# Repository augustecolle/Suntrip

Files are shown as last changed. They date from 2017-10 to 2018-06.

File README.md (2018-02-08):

# The Sun Trip
**Departure** mid june

**Deadline bike** february (preliminary inspection three months before departure, see Technical Regulations)

Auguste = :hear_no_evil:
Camille = :smirk_cat:
Baptist = :pig2:
Rien    = :car:
Mathieu = :construction_worker:

## Urgent TO DO's

1. ~~Start research on how to construct the roof :construction_worker:~~ DONE
2. ~~Do research on aerodynamic drag -- :hear_no_evil: :smirk_cat:~~ DONE
3. ~~Start research on best MPPT buck/boost converter for Li-ion technology -- :hear_no_evil:~~ DONE
4. Start research on batterypack -- :hear_no_evil:
3. ~~Make a technical drawing of frame :hear_no_evil: :smirk_cat:~~ DONE
4. ~~Read regulations in "Suntrip" folder -- :hear_no_evil: :smirk_cat:~~ DONE
5. ~~Order frame -- :hear_no_evil:~~ DONE
6. ~~present yourself :hear_no_evil:~~ DONE

## TO DO's

1. Compare different batteries on energy density (Wh/kg). Suntrip maximum 1100 Wh, 48 V.

   Nominal voltage as defined in datasheet, check if we can gain some capacity by choosing for the batteries with the lowest "nominal" voltage (a very underdefined term).

2. ~~Comparison of different solar panels.!~~ DONE

   Tandem regulations: max. 550 Wp and 3.05 m<sup>2</sup> __visible__. Max 1000 Wp in total. Working voltage must be <= 60 V.

3. ~~Passports: Each participant must hold before January 1st, 2018 a passport whose validity shall extend at least until February 1st, 2019.~~ DONE
 
4. Medical -- **before April 15th 2017** -- :hear_no_evil: :smirk_cat:

   - Obtain updated medical certificate in French or English confirming fitness for practice of endurance sports from a physician of their choice.

   - Signed medical record in annex of Adventure Regulations by our physician.

   - Vaccinations for travel in countries we will cross

5. Insurance (p23 of the Adventure Regulations)

6. Technical logbook (more info in early 2018).

7. Mapping an ideal route :hear_no_evil:

8. VISAs for all countries

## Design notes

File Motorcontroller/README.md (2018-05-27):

Motorcontroller
===============

I have to read much deeper into this matter but it seems like there are basically three options:

1. Trapezoidal control
2. Sinusoidal control
3. Field oriented control (a.k.a. the best in torque control and overall efficiency)

Phaserunner
-----------

The phaserunner looks like an evident choice, small, lightweight, state of the art, wide range of voltage and current, allows regenerative breaking, allows field weakening, ...

[check it here](http://www.ebikes.ca/product-info/phaserunner.html)

Fiel weakening test:

 - 12 amps field weakening gives 60 degrees Centigrade controller temperature and 18 amps phase current at no load. Motor goes from 41 km/h to 45.6 km/h no load speed.

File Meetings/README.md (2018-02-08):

Vergadering Soltech
-------------------
08/01/2018

Witruimte tussen cellen 2mm - max. 5mm meer opbrengst 2 a 3%

Plaatdikte te kiezen ifv sterkte/gewicht

Electronica minimale spanning voor te werken bepalend voor aantel seriecellen

Temperatuurscorrectie in MPPT voor batterijen laden?!

Cellen zelf solderen vs laten doen --> 200 euro

Solderen op ... 320? Vragen aan de fabrikant (SunPower)

Bypass diodes -> meer risicos bij laminatieproces want kabels moeten naar buiten gebracht worden

Misschien beter voor de hoeken, vooraan 6 -> 7 7 ... 7 -> 6 achteraan dan kunnen we hoeken afronden

Drie modules, 7 8 8 cellen op 7 cellen (breedte paneel).
-> 56 cellen 56 cellen en 49 cellen

3.41 Wp per cel
.612 Vp (check want enkel in datasheet waar onze cellen niet in staan)
5.8 Ap (check want enkel in datasheet waar onze cellen niet in staan)

Op welke termijn? 1 week als alle materialen zijn aangeleverd

Schokken zorgen voor micro barstjes, 2 lagen EVA op de back voor absorptie schokken. Eventueel schokdempers? Stefan zegt niet echt nodig, lijkt hem technisch moeilijk.

Zij kijken ook voor bestelling wit geanodiseerde platen.

Lijmen van alu plaat op structuur gevende plaat via dubbelzijdige foam, tec7, ... Ook voor vibratie absorptie

Ordegrootte prijs: 500 -> 900 euro als we zelf solderen, +200 als we niet zelf solderen

PVGIS -> maand per maand gemiddeldes zon

Offerte met cellen en zonder cellen aangevraagd.

Vergadering Raf Van Hulle
-------------------------
27/01/2018

* Windy app

    - Klopt dat ook met de werkelijkheid?

    - Bernard libellule, windscherm remde hem eigenlijk af

    - Windje zuigen --> mag niet volgens adventure regulations

  * Banden

    - Raf rijdt met Marathon Almotion in the Suntrip. 15000 km OKE, latex vulling 1x bijvullen.

    - City? ~15000 kilometer 

    - Worst binnenband voor snel band te vervangen

  * Claxon
    
    -  Raf heeft een megaluide noodclaxon op zijn handlebars

  * Batterij
  
    - Batterij wit schilderen? Als batterij in de zon?

  * Throttle
    
    - Duimregelaar die in postie blijft bij loslaten

  * Vocht problemen

    - Plastiek zakske meepakken om over cruciale onderdelen (elektrisch) fiets te trekken tegen condensvocht 's nachts

    - Connectoren naar motor e.a. verticaal monteren zodat er geen water in kan blijven staan (of niet laagste punt waar druppels blijven aanhangen)

  * Zonnepaneel
  
    - Raf zegt niets tegen paneel monteren omdat dat local hotspots geeft die paneelrendement beinvloeden (dus bv. Genasun niet ertegen monteren maar verticaal tegen een metalen latje of azo)

    - opm. geen koud water over uw paneel gieten als het heet is, door snelle afkoeling krijg je microcracks

    - opm. man van Duitsland zegt reken op ~3Wh/Wp opbrengst gemiddeld! Op piekdagen rond 4 a 4.5 Wh/Wp. Dit is op basis van zijn gemeten ervaring.

  * Fietstactiek

    - Als je weet dat je ergens moet wachten (grenspost, ferry, ...) peer dan vollenbak (elektrisch) daarnaartoe want tijdens wachten kan je batterij opladen.

    - Tunnels, als je niet veilig voelt contacteer politie voor escorte. Anders vraag burger om achter u te rijden met 4 pinkers.

  * Slaapplaats

    - Beter op een berg dan in een dal, voor 's ochtends opbrengst van het paneel te hebben.

  * Routing

    - Google maps werkt niet in China

  * Tent

    - MSR Freelite 2 (gebruikt Raf) is een tweepersoonstent

  * Mee te nemen

    - Deet meepakken!

    - Slot: Raf heeft Hiplok, heel licht

    - Waterzuiveringpomp vraag Alexander

    - Raf pakt ~10 kant en klaar maaltijden mee voor bv. in Kazachstan waar je lang geen groenten of fruit hebt of voor in nood.

    - Elektrolytische voedingssuplementen

    - Plaatjesboek met eten?

    - Asos koersbroek met zilverdraad tegen bacterien (gebruikt Raf)

    - Truitje winddicht vanvoor, vanachter ventilerend

    - Sportmasker met roetfilter, in Azie is dat naar tschijnt courant

    - Helm met vizier? Casco aero gebruikt Raf. Vizier is handig omdat vanaf 6 a 7 uur zonnebril te verduisterend is maar ge nog steeds vliegskes in u ogen krijgt.

    - Kamera express voor camerahouder op stuur

    - Universeel stekker (reisstekker)

Vergadering Groep T
-------------------
14/12/2017

  *  Hoe belangrijk denken jullie dat aerodynamisch design is als volledige omsluiting niet toegelaten is en kruissnelheid ~ 30 tot 35 km/u.

    Lynn denkt intuïtief wel dat aero design relevant is. Maar wat als niet volledig omsloten? Meer aero simulaties... Contactgegevens van aero-dudes wordt nog doorgestuurd

    Aerotape voor afplakken alles wat naden en kieren heeft

  *  Hoe hebben jullie de carrosserie ontworpen en gebouwd. Productieproces en materiaal?
 
    Carbon en met Indupol samenwerking

    Carrosserie is carbon, moet gebakken worden. Tussen de carbon platen wordt een schuim gespoten (varoa ofzoiets).

    Problemen met MDF bij het bakken --> zet uit waardoor mal vervormd

  *  Hoe worden de zonnecellen aangebracht op de carrosserie?

    Soltech, eigen laagje Suncat Solar LLC. Sunpower E60.
    Zonnepanelen worden geplakt met dubbelzijdige tape (M3, DM?), ze zijn dan al "ingekapseld" met een coating.
    De coating wordt door bedrijfje in Amerika gedaan. Stuur cellen op en ze worden gecoat teruggestuurd.
    Er wordt dan ook een "bus" (platte draad) aangebracht op de contacten aan de achterkant van de panelen 
    waar connectie mee kan aangebracht.

    Bij Soltech kunnen we coaten. Impact van coating op performantie van cellen (absorptie/reflectie van zonlicht) is niet gekend.
    Er is een thesis hierover, maar die is intern en is niet beschikbaar.

    Microsemi actieve bypass diodes. Het aantal cellen dat ge-bypassed wordt is afhankelijk van verwachte schaduw inval.
    2 cellen / diode voor panelen in slagschaduw van cockpit.
    4-5 cellen / diode voor panelen waar geen schaduw wordt verwacht.

  *  Is rekening houden met opwarming/koeling van de zonnecellen relevant?

    Gaten in het frame. Opwarming niet echt cruciaal. Panelen werden 90 graden tijdens stationair opladen.

  *  Keuze batterijcellen en MPPT?

    Panasonic, typenummer wordt nog doorgestuurd. MPPT is custom-made van ??? 
    Je kan spanning van cellen kiezen door layout van zonnecellen.
    Lynn raadt aan om spanning < batterijspanning te kiezen zodat je alleen boost MPPT nodig hebt.
    MGElectronics custom controllers MPPT, Oreon BMS? Lynn is niet zeker over Oreon. MGElectronics heeft ook eigen BMS.

  *  Voorspellen jullie de Wh/Wp (op dagbasis, weekbasis)? Hoeveel bedraagt de gemeten waarde?

    Dit wist Lynn niet te zeggen. Ze hebben in principe iets van 1.1 a 1.2 kW piek liggen en max. dat ze effectief gehaald hebben is ~ 0.95 kW.
    Zij deden continue weermonitoring. Zelfs zover als individuele wolken ontwijken.

  *  Welke simulatiesoftware gebruiken jullie voor de aerodynamische studie?

    Catia CAD, numeca simulatie

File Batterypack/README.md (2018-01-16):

The Battery Pack
================

Given the GenaSun MPPT GVB-8-Li-56.8V we have to design the pack for CV == 56.8 V.

Check datasheet of GenaSun in MPPT directory

Check [nknon](https://www.nkon.nl/)

Test [Vruzend](http://vruzend.com/). Cantactspray and fasteners?

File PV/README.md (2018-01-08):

All about PV
============

Regulations
-----------

550 Wp / 3.05 m^2  (~180 W/m^2, we want at least this, if not higher if we go below surface area 3.05 m^2 while still maintaining 550 Wp)

Flexible solar panels
---------------------

SunPower, high efficiency, low cost, DIY from individual cells.

1. [fragment](https://www.youtube.com/watch?v=KUU4UvGU8N0&t=2s) Check comments about using isopropyl alcohol to avoid bubbles
2. [fragment](https://www.youtube.com/watch?v=QD5SYrubR_E) Check comments for full description of the process
3. [fragment](https://www.youtube.com/watch?v=AgTDh4T9fro)

Sunpower
--------

Nominal cell power (Hp): 3.41 W 
Nominal cell area: 153.328 cm^2
Max. allowed area: 3.05 m^2
Max. allowed power: 550 Wp
Price/cell (Hp): 2.52 dollar ~ 2.13 euro (exchange rate of 20/12/2017)
Orders come in packs of 150 cells

(Max. allowed area)/(Nominal cell area) = 198 cells (truncated)
(Max. allowed power)/(Nominal cell power) = 161 cells (truncated). Since this is lower than the cells needed to cover the max. area, this means the Hp series (lowest price, least efficiency) qualify for still getting maximum power.
Price for 300 cells: 756.0 dollar
Price for 1200 tabs: 84.0 dollar

Solar cells
------------

12.5 cm x 12.5 cm
550 Wp / 3.41 W = 161 cellen.
161 x (12.5 cm)^2 = 2.515625 m^2

162 cellen
-----------
12.5 cm x  6 = 75.0 cm  ->  80 cm
12.5 cm x 27 = 337.5 cm -> 340 cm
--------------------------------
             = 2.53125 m^2 -> 2.72 m^2 

160 cellen
----------
12.5 cm x  5 = 62.5 cm  ->  67.5 cm
12.5 cm x 32 = 400 cm   -> 402.5 cm

161 cellen
----------
12.5 cm x  7 = 87.5 cm  ->  92.5 cm
12.5 cm x 21 = 262.5 cm -> 265.0 cm

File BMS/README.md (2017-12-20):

Battery Management System
=========================

Orion
-----

[BMS jr](https://www.orionbms.com/products/orion-bms-jr/)
[BMS jr utility](https://www.orionbms.com/manuals/utility_jr/)

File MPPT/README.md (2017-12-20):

 
[link](https://www.bruceschwab.com/solar-power/solar-charge-controllers/)

[link](https://www.re-innovation.co.uk/blog/2011/open-design-charge-regulator-project/)

[link](http://tahmidmc.blogspot.be/2013/01/using-high-low-side-driver-ir2110-with.html)

MG Electronics
--------------

[MG Solar MPPT](https://www.mgenergysystems.eu/rd/mg-solar-mppt/#specifications)

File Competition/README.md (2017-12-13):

Andere deelnemers uitchecken, alleen personen vermeld die specs. van hun fiets hebben gepost.

Maroccan Team
===============

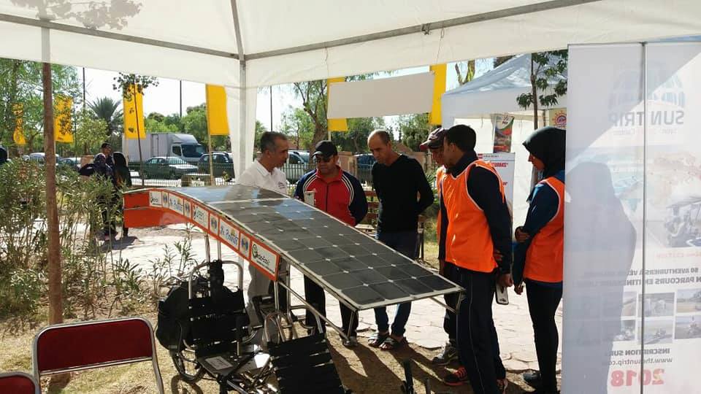
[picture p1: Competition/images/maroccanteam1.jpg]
bikephoto1

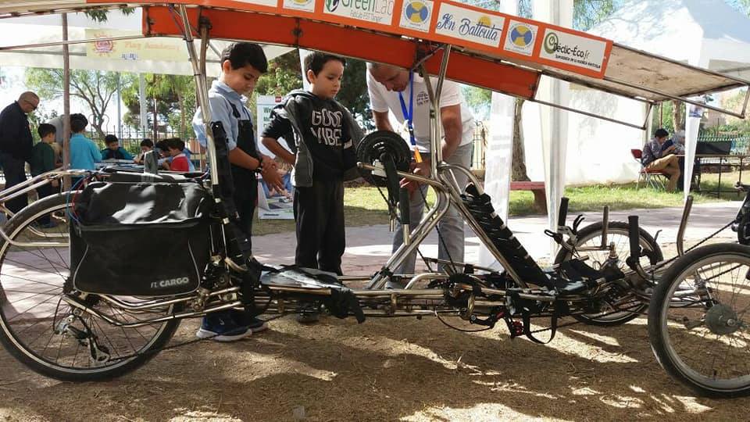
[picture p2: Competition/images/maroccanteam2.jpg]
bikephoto2


W W Ching on an eZeebike
========================

- [forum post](http://thesuntrip.forumactif.org/t416-w-w-ching-on-an-ezeebike)
- [bike specs.](http://ezeebike.com/gallery/longabike-2/)
    - Brushless Planetary gear Motor
    - Battery : 19Ah to 34 Ah
    - Controller: 36-48 V, Max 25 Amps
    - Motor Rating: EU 250W, USA 500W, AU 200W
    - Option : 260 W Solar PV roof

Michel Bamps
=============

- [forum post](http://thesuntrip.forumactif.org/t417-traction-animale-propulsion-solaire)
- bike specs.
    - [raptobike mid-racer](http://webshop.raptobike.nl/bikes/mid-racer.html)
    - [FG40 Cystalite motor](http://www.crystalyte.com/The%20G%20motor%20series.htm)

Bernard Cauquil
===============

- [website](http://bernardcauquil.fr/parrainage/index.php?route=product/category&path=20) met alle details van zijn fiets!
- [blog](http://www.sunrider.fr/)
- hij doet mee aan een [wedstrijd](http://bikingman.com/en/bikingman-oman/) in februari (met zonnefiets?)
- [strava](https://www.strava.com/athletes/14980880) Hij is precies goed getraint.
- [youtube filmtje](https://www.youtube.com/watch?v=NAL1kyalmh8), trike w. fat tires, solar panel roof and he talks about a Tandem, is this a name, a bike? The trike in the movie is just a prototype. Anyway what looks very interesting is the way he installed the motor. It's just below the seat and the rotor is connected to the chainrings. See the picture below for his design in 2015, the configuration is clearly different in the trike set-up but has the same working principle. The first thing advantages I can think of, you can easily migrate to the max. eff. point of the motor by choosing an appropriate gear ratio determined by your cruising speed.

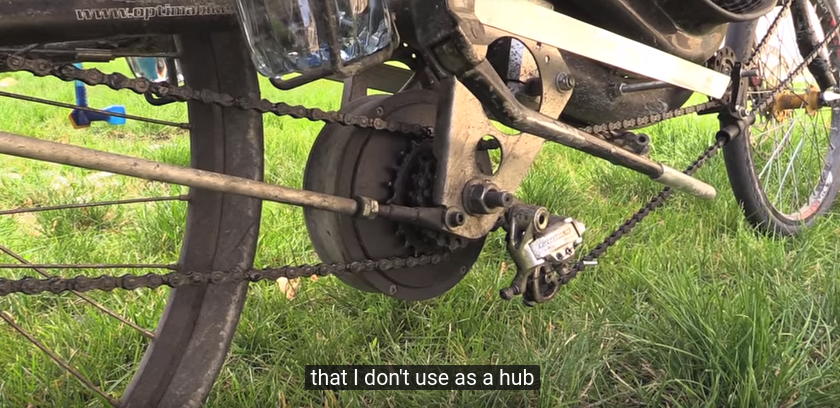
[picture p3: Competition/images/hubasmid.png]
hubmid


specs

- [finish - youtube](https://www.youtube.com/watch?v=S6kONVGS2qk)

- [tech. - youtube](https://www.youtube.com/watch?v=WUoEbcKhzgo)

Raf Van Hulle
=============

2015 fiets:
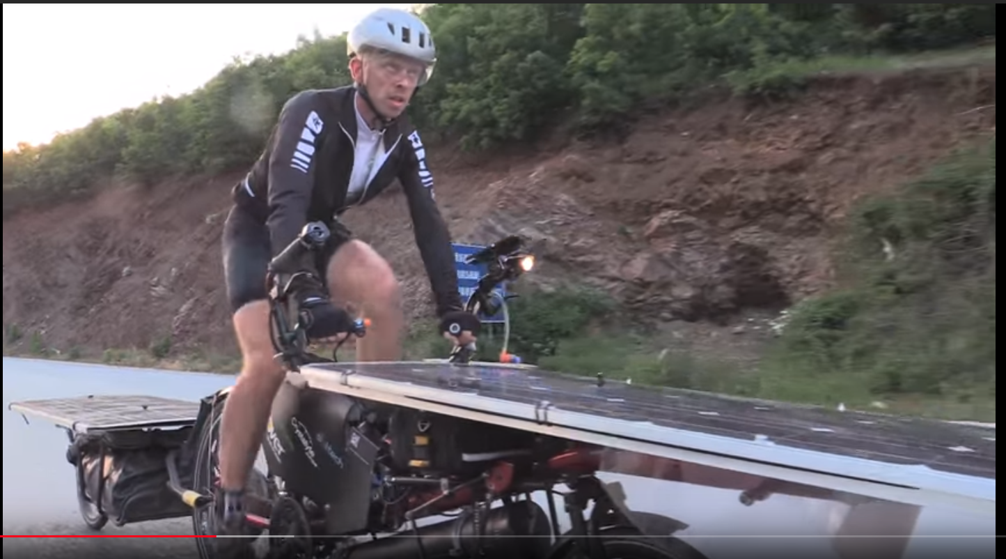
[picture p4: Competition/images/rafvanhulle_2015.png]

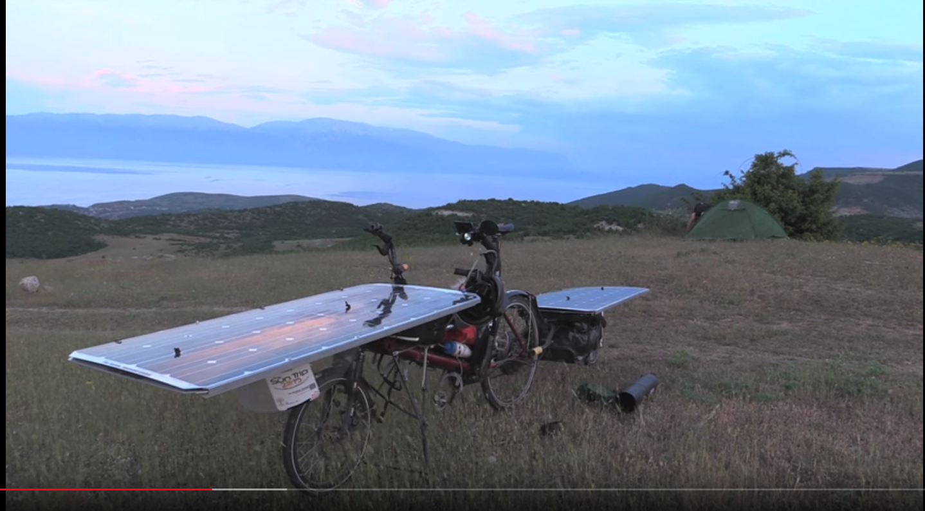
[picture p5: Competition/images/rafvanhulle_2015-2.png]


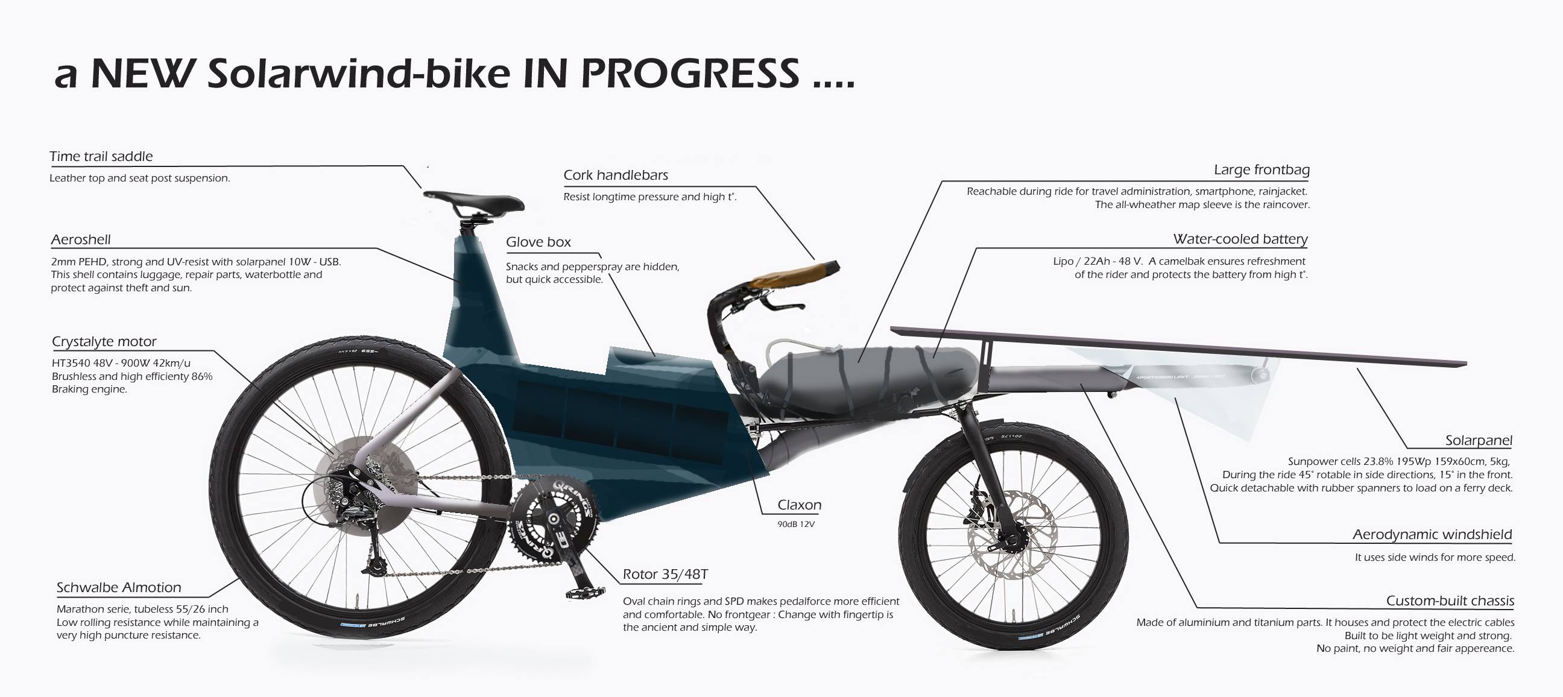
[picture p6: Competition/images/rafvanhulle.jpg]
raf


Jose
=====

Eervolle vermelding voor hilarisch niet relavante links in zijn [post](http://thesuntrip.forumactif.org/t421-hello-to-everyone-from-huelva-spain)

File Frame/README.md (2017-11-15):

Frame
======

Freewheels
----------

Current freewheels are of the brand [Dicta](http://www.dicta.com.tw/), according to most reviews they basically suck.

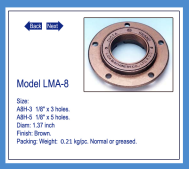
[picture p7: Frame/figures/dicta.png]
Dicta


Auguste ordered new ones from White Industries, the ENO freewheel but optimized for durability and rough use as can be found on sickbikeparts "heavy-duty front freewheel". On the White Industries website:

> Traditionally, freewheels have been considered a disposable component and one that should be replaced on a regular basis. It is our belief that when you invest in your drivetrain you should expect your gearing to be of sufficient quality and durability to allow more time for riding and less for repairing and replacing components.  We set out to create and manufacture a freewheel that would be durable, reliable, and easily maintained.

[ENO](http://sickbikeparts.com/front-freewheel-heavy-duty/)

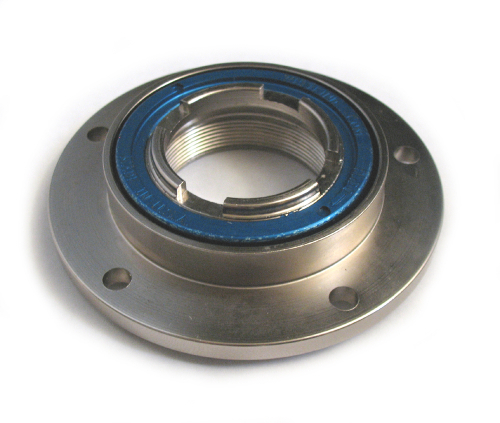
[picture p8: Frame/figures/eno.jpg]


Sizing
------

Rear dropouts inner length: 137 mm

Rear dropouts outer length: 154 mm

Fairing
-------

Aerodynamic [fairing](http://t-cycle.com/windwrap-fairings-c-68/complete-fairing-kits-c-68_67/wgx-onepoint-full-fairing-kit-p-195.html) for trike?

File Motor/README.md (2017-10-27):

Motor
=====

For the moment I'm only looking at efficiency curves. I mention peak efficiency followed by an indication of sensitivity by mentioning the RPM range for which the efficiency > 80%.
Wheel size = 20"

Hub motors
----------

### Grin All-Axle

87.9% [333.4 - 485.9] [80.0 - 80.5] a range of 152.5 RPM

### Grin Hub

Same motor

### 9C+ 2705

87.9% [387.6 - 579.7] [80.0 - 80.6] a range of 192.1 RPM

Other 9C+ motors have less performance

### Bafang BPM

82.8% [280.5 - 360.1] [80.0 - 80.0] a range of 79.6 RPM

### [294.0 - 401.8] [80.0 - 80.3] a range of  

### Mac 10T

### 

### BMC V2, V3, V4

High end geared hub motors. 600w overvolting capacity to 2500 watts. The BMC is a larger (8lb) geared hub motor, designed to be more efficient and have a better power-to-weight ratio than a gearless (direct-drive) motor.  (Read our [review](https://www.electricbike.com/bmc-hub-motor-review/) here)

### MAC Motor (BMC clone)

Very similar to the BMC but not as high quality, so cannot withstand high power and have the same reliability as the BMC.

### Dapu Hub Motor

A new hub motor used on production bikes such as the Neo Jumper and City Commuter. It is small, wide, and puts out a maximum of 750 watts.

### Crystalyte ( HS35 /  HT35)

A recently released direct drive motor weighing in at 16 pounds (Read our [review](https://www.electricbike.com/crystalyte-hub-motor/) here)

### Cute Motor

A small planetary geared motor. 5 lbs, and capable of running 800 watts. Figure around 20mph top speed on a cute powered E-bike. Very small nice looking motors, can barely tell bike has a motor.

### Bafang

A small planetary geared motor very similiar in size and performance to the Cute motor.

### 9-Continents (9C)

A gearless brushless motor weighing in around 15 pounds and capable of putting out serious power when over volted. A reliable and solid motor. (read our [review](https://www.electricbike.com/9c/) here)

### BionX

A sleek  system, but expensive and made from all proprietary components, making it hard to upgrade controller or battery. Comes in 250, 350, and 500 watt configurations.

### BPM hub motor

A larger geared hub motor (about same size as bmc or mac) that puts out a maximum of 500 watts.

### Golden Motor (magic pie)

A heavy DD motor capable of putting out good power when over volted.

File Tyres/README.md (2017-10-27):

Tyres
=====

Solid tyres (#I don't want a flat on the rear wheel)
----------------------------------------------------

Solid tyres have a higher rolling resistance but never go flat and are lightweight, the have a life expectancy of 8000 km according to brand [Tannus](https://tannusamerica.com/). A [youtube video](https://www.youtube.com/watch?v=QIvDEdxg-b4) shows it's worn out at around 2500 km, however a user's comment contradict this. [Greentyre](http://www.greentyre.com/bicycle-tyres.php) also sells solid tyres but yet again I find [dissatisfied costumers](https://www.camcycle.org.uk/newsletters/75/article18.html). Then there is another much more recent player on the market, [Nexo tires](https://www.nexotire.com), yet again I don't seem to find good reviews.

Tubeless tyres
--------------

Schwalbe believes this is **the technology**, from their website:

> Tubeless tires provide clear advantages in speed, comfort, grip and puncture protection. They avoid unnecessary friction between tires and tubes, which reduces the rolling resistance even more than with super light competition tires.  Tubeless tires can be used with a lower inflation pressure without compromising performance. That brings clear advantages in comfort as well as clearly more control in critical situations and on bad surface trails. At the same time, tubeless systems provide a high puncture protection. The danger of blowouts is clearly reduced. A sudden loss of air pressure by burst tubes or valve tear off is excluded. What is more, tubeless systems function perfectly together with puncture protection liquids. Punctures are re-sealed within milliseconds.  

However, they do not have the equivalent of the marathon plus protection (rated the maximum score of 7) in the tubeless category.

Clinchers tyres
---------------

Seems like [Schwalbe marathon plus](https://www.schwalbe.com/en/tour-reader/marathon-plus.html) tires seem the way to go. Mileage for the marathon tyres (not the marathon plus) seems to be in between 6000-12000 km.

[Continental touring plus](http://www.continental-tires.com/bicycle/tyres/city-trekking-tyres/touring-plus) doesn't sell in 20" format, as with Vredestein and Maxxis (although Maxxis has the creepy crawler but that just doesn't look like it).

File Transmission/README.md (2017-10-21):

# Transmission - chains

Although the Connex catalog seems more extensive all the threads I read on public fora indicate a better performance from the KMC chains.

The optimal combination seems to be KMC chain with Wipperman Connex master link.

[Example Wipperman Connex](https://www.amazon.com/Wippermann-Connex-11-Speed-Stainless-Steel/dp/B010DRJVOA?tag=viglink20255-20)
[KMC chain selection](http://www.kmcchain.eu/CHAIN_CHOICE)

# Transmission - gears

Derailleur system
-----------------

This system seems to have the most advantages, not surprisingly since everybody in the professional race circuit uses this. Derailleur system should be well maintained in order to achieve high efficiency. 

| Transmission Type | Average efficiency at 150 W |
|:---:|:---:|
| Derailleurs | 93 - 95 % |
| 3 speed Gear Hubs | 92 - 95 % |
| 7 & 14 speed Gear Hubs| 89 - 91 % |

> Efficiency testing of bicycle gearing systems is complicated by a number of factors - in particular, all systems tend to be better at higher power rates. 200 Watts will drive a typical bicycle at 20 mph, while athletes can achieve 400W, at which point efficiencies 'approaching 98%' are claimed. Source: [wiki](https://en.wikipedia.org/wiki/Bicycle_gearing#Efficiency).

Pinion
------

From their website:

> Thus the efficiency of a Pinion transmission is between a high-quality hub transmission and a new chain shifter running absolutely straight from front to back. If a chain shifter is dirty and skewed, the efficiency of Pinion is better.

Rohloff
-------

Max. efficiency comparable with derailleur system

Nuvinci
-------

Nothing known about efficiency, company seems not to share this information.

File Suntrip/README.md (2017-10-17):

# Sun trip

## Challenges:

1. **Solar Challenge**

2. **Adventurer - Blog and Social Media Challenge**

## Questions on reading the regulations

1. Field weakening on BLDC motors allowed?

2.

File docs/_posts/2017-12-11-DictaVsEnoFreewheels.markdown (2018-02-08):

---
layout: post
title: "Free Wheely"
date: 2017-12-11
background: "/img/IMG_20171211_182026.jpg"
---

First diagnose of our patient revealed very wobbly chain rings on both the captain as the stokers position. You could quite easily push the chain rings half a centimeter out of the chain line. On closer inspection it seemed to be caused by the Dicta brass freewheels. Not wanting to replace the chain line every 5 kilometers we decided to investigate the availability of somewhat more qualitative freewheels on the world wide web. Sickbikeparts sells ENO heavy duty freewheels, tempted by their shiny look we ordered them immediately.

I must say, it was quite some trouble to get them properly installed. The ENO freewheel has M5 holes and our spider has M6 bolts so we had to adapt one or the other to make the whole thing fit. We started of by trying to drill a hole in the freewheel, broke our drill and didn't even manage to scratch the surface. As luck would have it, we have a mechanical department just 40 meters from my desk at KU Leuven, hooray! Those guys have somewhat the same equipment in their lab, but always at least thrice as big and twice as durable. Their column drilling machine was quite a showoff and they had carbide tipped drills but only managed to produce more sparks and no hole, the concept of heavy duty started dripping in. After searching half an hour for cobalt drills we decided to give up and adjust the spider instead of the heavy duty freewheel. We drilled some new holes, freed up some space with the lathe for a better fitting and we are very happy with the result. No more wobbly chain rings and a solid ratchet sound, we love it.

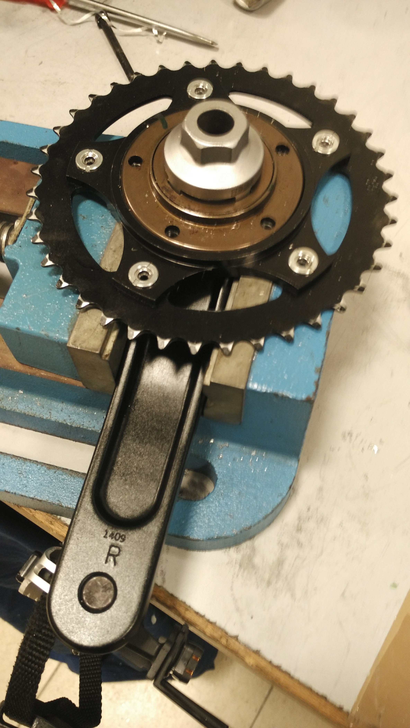
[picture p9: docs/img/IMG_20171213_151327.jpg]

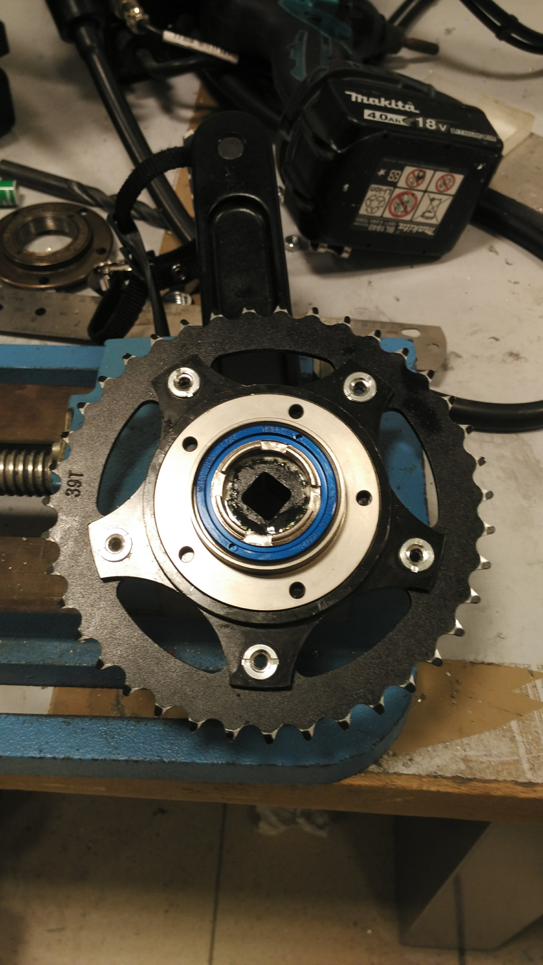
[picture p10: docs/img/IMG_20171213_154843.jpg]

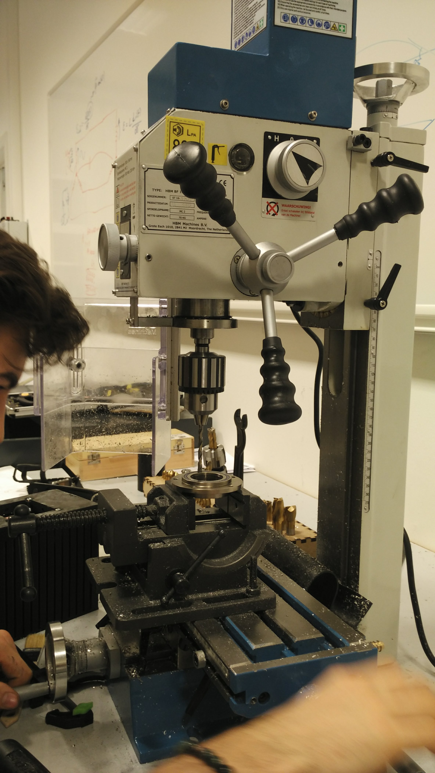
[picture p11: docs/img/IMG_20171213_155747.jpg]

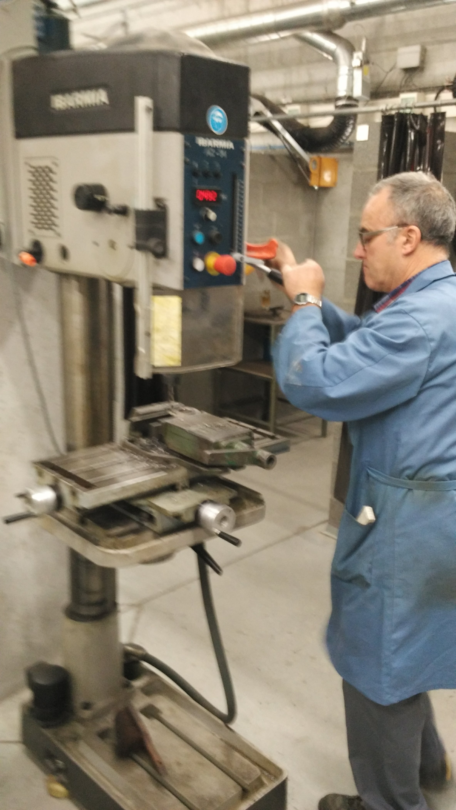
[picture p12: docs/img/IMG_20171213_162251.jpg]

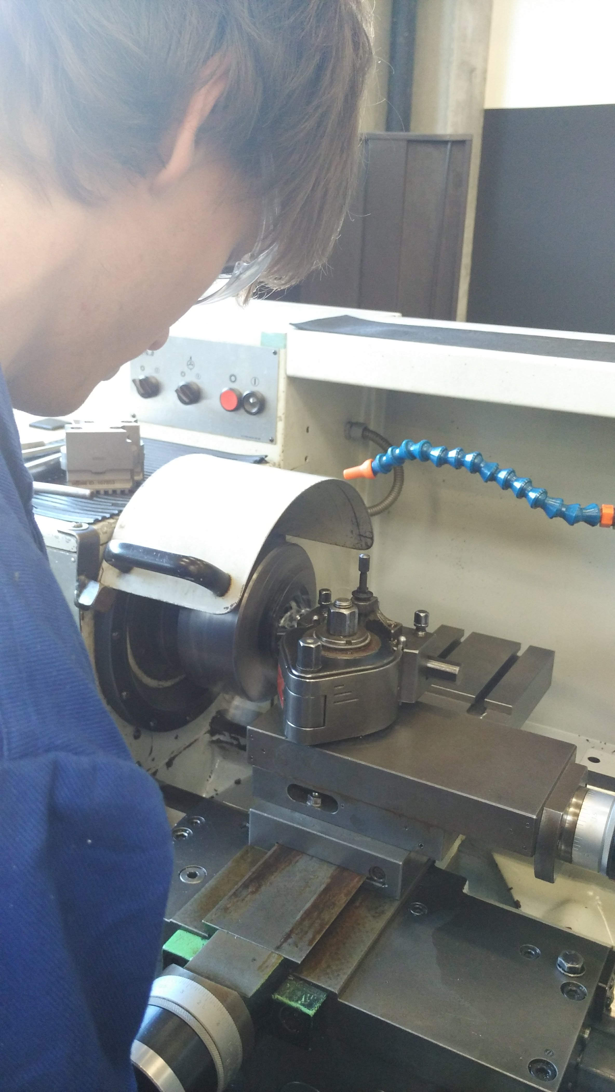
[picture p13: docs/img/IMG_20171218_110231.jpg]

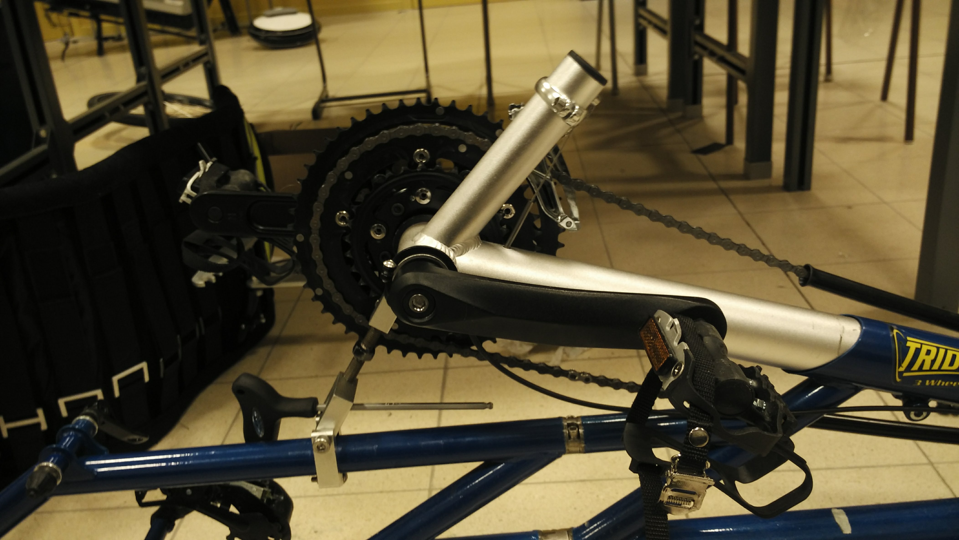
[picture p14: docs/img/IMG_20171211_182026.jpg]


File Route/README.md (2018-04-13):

# Route

_sun trip organisers:_
  - if there are checkpoints it will be only in China, and only if Chinese authoritories ask that.
  - pour clair et direct seuls les trois jours du prologue en France seront assistés, avec un accueil chaque soir pris en charge, et aussi pour votre arrivée à Canton.

At this time, we aim at holding the official departure in Lyon on June 15 or 16 (this is provisional information).

Then we should spend 3-4 days together on a prologue:
one night near the Bourget Lake (Savoie), near Aix-les-Bains & Chambéry. 
one night in the Bauges mountains (Savoie). 
one night in the Aravis mountains (Haute-Savoie), near Le Grand Bornand. To be confirmed. 
and then, the final base camp in Chamonix. 

The start proper should take place in Chamonix on June 19 or 20

## "Official accomodation in Russia"
  - [Kursk](http://www.gostevoi-dom-na-sutki.ru/) No campsites. Hostel with good reviews ~9 euro.
  
  - [Belgorod](https://www.hostelkorona.com/) No campsites. A few hostels. [this](https://www.hostelkorona.com/) one has good reviews and is one of the cheaper options (~9 euros)
  
  - [Vorozneh](http://hostvrn.ru/kemping-v-voronezhe/) Cheap hostel/camping (~4 euros). Nice website.
  
  - [Balashov](http://turbaza-hoper.ru/domiki.html) Looks like a very nice campsite, I don't see rates for tents but for a "summer house" it is about 7 euro per person.
  
  - [Saratov City Hostel](https://www.booking.com/searchresults.en-gb.html?aid=1288283;label=metagha-link-mapresultsBE-hotel-1930131_dev-desktop_los-1_bw-30_dow-Sunday_defdate-0_room-0_lang-en_curr-EUR_gstadt-8_rateid-0_cid-85;sid=9ed1b5c0e05c2b57c51e58a33742861a;checkin=2018-05-13;checkout=2018-05-14;city=-2996563;highlighted_hotels=1930131;hlrd=with_av;keep_landing=1;redirected=1;source=hotel&utm_campaign=BE&utm_content=los-1_bw-30_dow-Sunday_lang-en_curr-EUR_gstadt-8_rateid-0_cid-85&utm_medium=mapresults&utm_source=metagha&utm_term=hotel-1930131&room1=A,A,A,A,A,A,A,A,;) No campsites nearby. This is the cheapest hostel ~7 euro's, has only 4 reviews but 3 of them are positive.

## Route segments:

GraphHopper for start-finish (Chamonix - Canton)

    - distance       : 12150 km
    - elevation gain : 68882 m

Sum of indiv. segments:

    - distance       : 11941 km
    - elevation gain : 63145 m

- Chamonix - Uralsk : Graphopper, not checked

- Kazachstan : Uralsk - Zahrkent (approx. 3000km)
    - possible route through Kazachstan on what looks like paved roads all the way.
      Bicycling touring seems ok on section between Shymkent and Almaty, relatively "popular"
      No information on the other part...
      *TODO* Check if this is shorter than norther route (Graphhopper).
      
      [Road conditions](https://caravanistan.com/transport/driving/kazakhstan/)
      Overall conclusion, looks good for the most part for our route!
        - Saratov (RUS) - Urask: degraded road surface (potholes)
        - Uralsk (Oran) - Aktobe : new tarmac (2015)
        - Aqtobe - Aralsk via E38: Excellent quality tarmac. From Karabutak to Aralsk there are now at least 3 petrol stations operating between those towns. One after 112km, one near Irghiz (around 190km after Karabutak), and one at 380km.
        - Shymkent – Turkestan – Kyzylorda – Aralsk – Aqtobe: New road (2014).  Excellent quality tarmac.
        - Shymkent – Taraz – Shu – Almaty: New road (2014).
        - Saryozek – Altyn Emel – Khorgos – Urumqi: Decent.

- [Kiev-Krakow](https://www.bikemap.net/en/route/3290130-kiev-krakow-927km-1680hm/#/z11/49.9887595,20.1811981/terrain)
  From Krakow east, mainly along the national road parallel to the E40. The section between Lancut en Pryzeworst seems to be 2 lane road with no shoulder so routed along smaller roads for that small part.
  
  In Ukraine it seems people cycle on the E40 highway! Strava shows activity on the road and I spotted some on [google maps](https://www.google.be/maps/@50.0385691,25.1370347,3a,75y,14.35h,86.64t/data=!3m6!1e1!3m4!1sTIjiASKU5MOwoemVcqnwdA!2e0!7i13312!8i6656?hl=en), look at this [badass](https://www.google.be/maps/@50.0559231,25.1477143,3a,75y,146.42h,68.25t/data=!3m6!1e1!3m4!1sXR9xV-b-WOuMpLzcBXRo7Q!2e0!7i13312!8i6656?hl=en). After extensive google street view inspection it seems that [locals](https://www.google.be/maps/@50.1118557,25.1962285,3a,75y,167.17h,62.94t/data=!3m6!1e1!3m4!1s7tTR2epj1cqReqeXDy54yg!2e0!7i13312!8i6656?hl=en) cycle on the E40 so this is probably allowed. [clip](https://www.youtube.com/watch?v=D1hZOart86w) of the E40 between L'viv and Kiev.
  Detours seem possible put alternative roads seem very bad and full of potholes (google maps).
  The highway in the north, E373, seems very smooth and quieter but it is a huge detour...
  
- [Shanghai - Kazachstan](https://www.bikemap.net/en/route/818839-shanghai-to-kazakhstan/#/z6/41.1124688,101.3378906/google_roadmap)

- China:
    - (K)Horgos-border crossing to Urumqi via G312/G30. Apparently highway is closed officially closed to cyclists. Several blogs mentioning ignoring signs and riding through [1](https://www.crazyguyonabike.com/doc/page/?page_id=82269), [2](https://brakingboundaries.org/2014/06/25/scenes-road-urumqi-zhangye/), [3](http://www.twistingspokes.com/we-cycled-to-china-everything-changed/), [4](https://ontheroadagain.travellerspoint.com/82/). In fact all posts about Almaty - Urumqi seem to take the G312/G30...
      - added GPX track using graphopper, had to set profile to cars to get track along G30 as bicycle profile will not take this...
    
    - [Xinjiang province](http://www.14degrees.org/china-xinjiang-province/) (Khorgos-border to Gansu province border). Follows G312 all the way. With description of road and accomodations along the way.
    
    - [Urumqi - Xian](https://www.crazyguyonabike.com/doc/?doc_id=3112) blog of Urumqi - Xian route. Mentions taking the  (toll) "express way" that runs parallel to G312 although technically no cyclists allowed.
    
    - [Xinjang, Gansu](https://cycling4cancer.wordpress.com/2013/08/23/epic-distances-through-western-china-traversing-xinjiang-gansu-and-qinghai/) mentions riding on the G30 express way instead of the parallel G312.
    
    - Wuwei - Xi'an (Liantan) : checked with Google maps (sattelite), looks asphalt all the way. Note that Wuwei - Xi'an over Lanzhou is similar in distance but has much more height meters, so going via Zhonwei en Pingliang is favoured. Looking on strava it seems that in and around Lanzhou cycling is more popular.
    
    - Xi'an (Liantan) - Denzhou : checked with Google maps sattelite view
    
    - Jingzhou (Try to take the [ferry](http://georgethecyclist.blogspot.be/2009/10/zhijang-china.html), bridge detour is approx 150 to 200 km).
    
    - Denzhou - Chenzhou : check with Google maps sattelite
    
    - Chengzhou - Guangzhou (finish) : Graphopper, not checked. Strava, not checked. Note that strava gives half the elevation gain. (How accurate is this?)

## TO DO:

1. Check the raw_route manually for forbidden border crossings, check on paved roads and check if all roads are doable with a bicycle.

## Optimization

Least relief, most sun, shortest distance, least borders to cross?

After watching Sun Trip 2013 we definitely want to prefer paved roads to unpaved ones.
Especially since dodging stones and potholes is more difficult on a trike.

## Started routing :hear_no_evil:

1. ~~Started to make a track based on the profile of a "racingbike" on [graphhopper](https://www.graphhopper.com/). This profile prefers "roads", which I interpret as paved. It is the only route planner I found which is able to plan such a long distance and it comes pretty close to the straight line in Google Earth.~~

~~I converted the track to .kml to view in Google Earth and Google Maps.~~
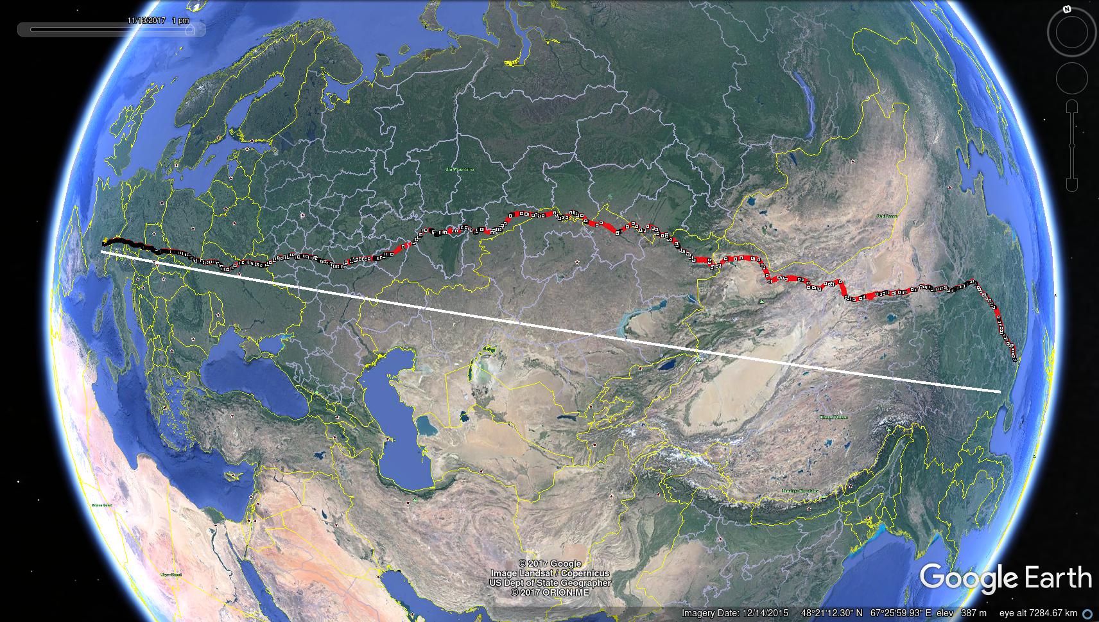
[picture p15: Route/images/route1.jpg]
track1


Problem: check the route manually for bad things as crossing the border with Belarus, manual rerouting is needed. Also some paved roads are highways, for example:

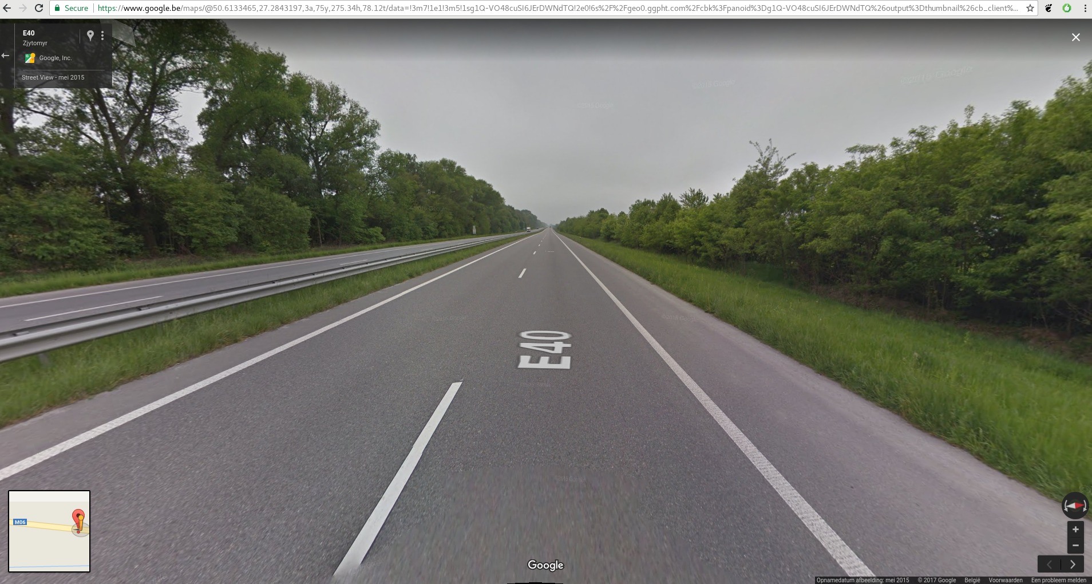
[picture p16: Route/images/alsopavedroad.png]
pichighway


2. :smirk_cat: Made new graphhopper that starts from correct starting location: Chamonix, France

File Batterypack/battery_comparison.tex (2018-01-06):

\documentclass[11pt]{article}

\usepackage{graphicx}
\usepackage{amssymb}
\usepackage{amsfonts}
\usepackage{amsmath}

\setlength{\parindent}{0pt}

\begin{document}

\section*{Battery cell comparison}

\subsection*{Battery types}

\begin{tabular}{lcr}
    IMR, LMO &--& Lithium Manganese Oxide \\
    INR, NMC &--& Lithium Nickel Manganese Cobalt oxide \\
    NCA      &--& Lithium Nickel Cobalt Aluminum oxide \\
    NCO      &--& Lithium Nickel Cobalt Oxide \\
    LCO, ICR &--& Lithium Cobalt Oxide \\
    IFR, LFP &--& Lithium Iron Phosphate \\
    NCR, NNP &--& Lithium Nickel Cobalt Aluminum oxide \\
    LTO      &--& Lithium Titanate \\
    Li-S     &--& Lithium Sulfer
\end{tabular}

\subsection*{Comparison}

\begin{table}[h!]
    \centering
    \begin{tabular}{c c c c c c c}
        \hline \hline
        Brand & Type & DC res. & AC res. & nom. V & nom. C & real C\\
        Panasonic & NCR20700 & 
        \hline
    \end{tabular}
    \caption{Comparison of different batteries}
\end{table}

\end{document}

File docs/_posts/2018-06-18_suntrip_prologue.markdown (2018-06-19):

---
layout: post
title: "Prologue"
date: 2018-06-18
background: "/img/IMG_20180618_124331_HDR.jpg"
---

At 3 A.M. we gathered at the campus in Ghent to drive to lyon with the bike on a trailer.
Jack, another suntrip participant, joined us and the three of us were driven by Tom down to Lyon.

We were one of the earlier participants to arrive and after re-assembling our bikes and passing the technical control we set up camp as other participants showed up.

The next day we said goodbye to Tom and thanked him for all his efforts. Almost all participants had arrived and the field was full of solar bikes and tents. 

At midday there was a reception organized by the domain owners and after a briefing in the afternoon we set off to “place des terraux” in the city center for a public suntrip event. There were a lot of activities there about the suntrip and the Chinese culture.

We had a fun ride back to the campsite together with Jack, including an accidental detour with a nice view over Lyon. As the night fell we were puzzled about some BMS (Battery Management System) issues.

The next day was the first real suntrip day. After another visit and show off at “place des terraux” the prologue was started with the first cycling etappe to a campsite near Aix-les-bains. The ride was super nice, a lot of sunshine and flat roads translated into swift riding. We kept bumping into other participants as everyone was taking similar roads.

When we arrived at the campsite Auguste and I were selected for a photoshoot with our bike at the lakeside, which was quickly followed by a swim in the lake itself.

The next day we cycled to several other suntrip showcase events. In the afternoon we had our first real long climb over a pass with the bike. It was pretty tough and we were rather slow on the steep ascent, being overtaken by a few other suntrippers.
Jack who was riding with us took control over the bluetooth speaker and played some motivational tunes.

For the last cycling etappe of the prologue we rode the next day to chamonix, again together with jack.
On the scenic descent towards the lake of annecy we passed a lot of baffled looking cyclists. We had lunch in Cluses, in front of a supermarket.

In the afternoon we successfully tested our field-weakening phaserunner. The last climb to chamonix was brutal. Just outside of Servoz the slope kicked up so steep that we had to push the bike for a few tens of meters.
Luckily it quickly leveled off and we had a very scenic ride through the chamonix valley.
After a photo session by national geographic journalists we arrived pretty early at the gite booked by the suntrip.
Only 29 of the 45 participants made it in time for dinner at 21 PM.

The program for the last day of the prologue was another public showcase on the town square of chamonix and a cable car ride up the mountain side for a photoshoot with the Mont Blanc and the chamonix valley.
Around noon Auguste’s colleagues arrived by car, carrying some repair/upgrade tools which were promptly put to use after lunch.













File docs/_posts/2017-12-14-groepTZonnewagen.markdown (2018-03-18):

---
layout: post
title: "Meeting with solar car team from Group T"
date: 2017-11-14
background: "/img/solar1.jpg"
---

Ended with a third place in the World Solar Challenge (for solar cars), visiting our colleagues from Group T sure should be an interesting opportunity to discuss ideas on solar panels, aerodynamic design and everything in between. Not wanting to miss the opportunity to have a glimpse at the solar car, 2 of my colleagues joined us for the too-early-in-the-morning train to Leuven. As we arrived in the station, Lynns message arrived in my mailbox explaining her fellow team members had some jet-lag related too-early-in-the-morning issues and they could not make it in time. Luckily café Entrepot serves cappuccinos with decent steamed milk and we were four persons which means we had to play cards, time suddenly flew by too fast. Lynn called, she arrived at our meeting point.

The solar car definitely is a nice piece of machinery. We could look at everything, ask anything but sure were not allowed to touch anything as one of my colleagues quickly found out while inspecting the silica coating on the solar cells. Lynn told us all about solar cells (theirs have an efficiency of ~36%), highly efficient MPPT converters made by MG Electronics and silica coatings from a guy living in the States with a patented technology (he makes the coating in his garage). She also told us their budget was about a 150 times ours, which quickly sunk in when she started estimating the cost of the different components. Before leaving she gave us contact details which she guessed might be useful for our project, I was a little ashamed we didn't bring anything to give in return. It sure was an interesting start of our day, thanks again Lynn!


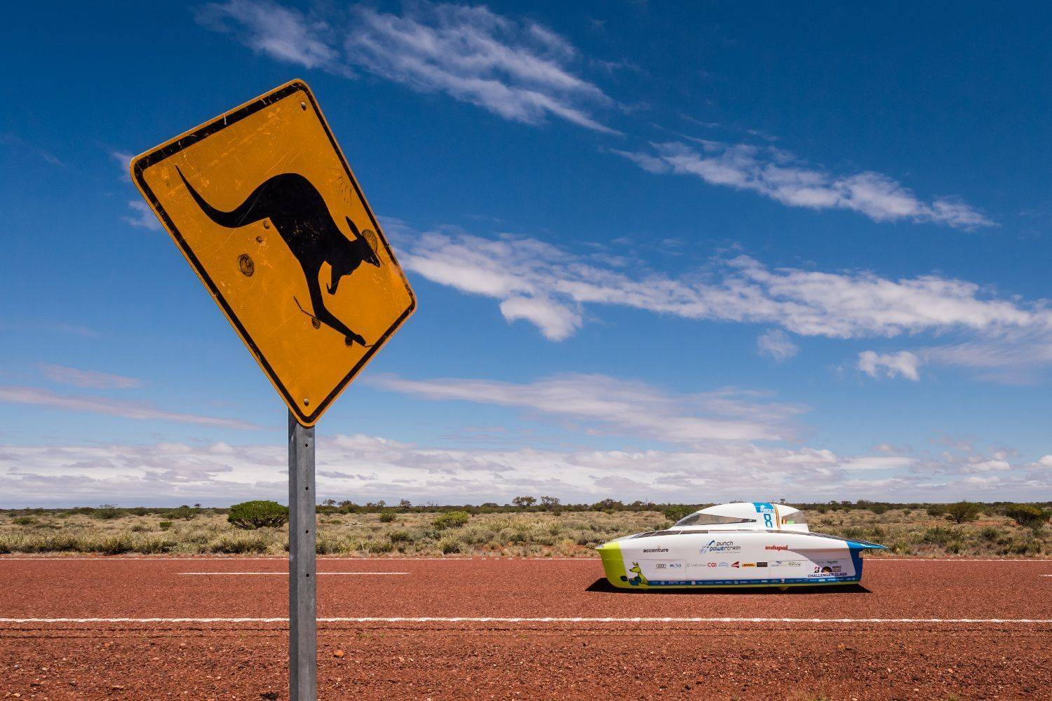
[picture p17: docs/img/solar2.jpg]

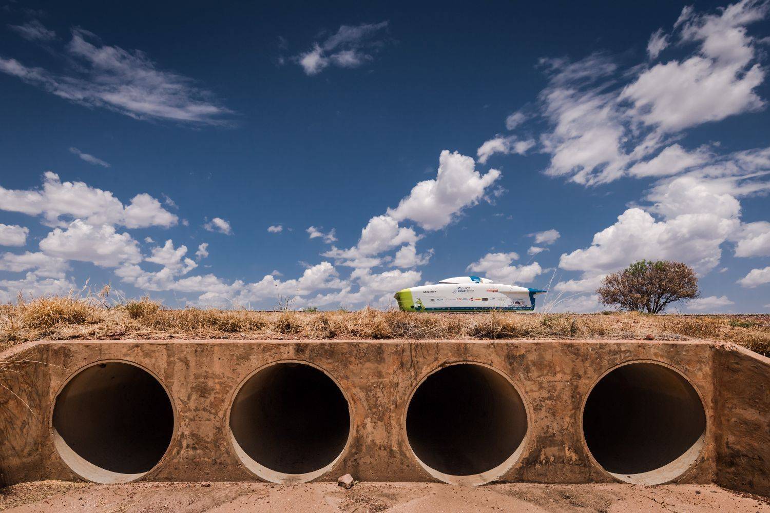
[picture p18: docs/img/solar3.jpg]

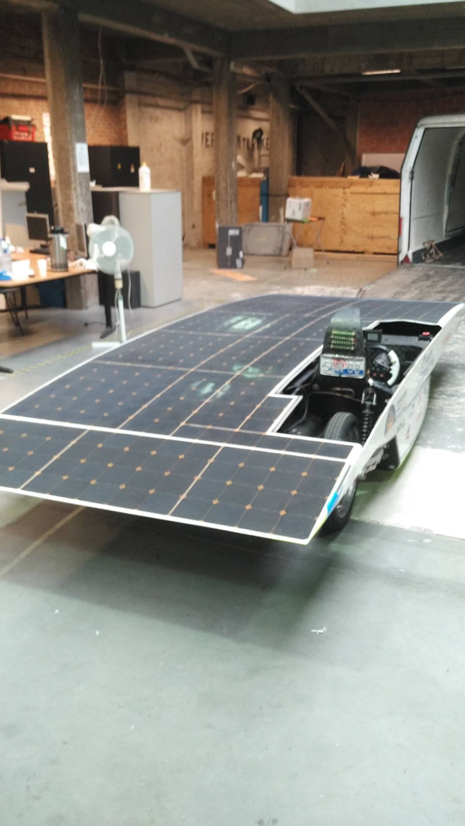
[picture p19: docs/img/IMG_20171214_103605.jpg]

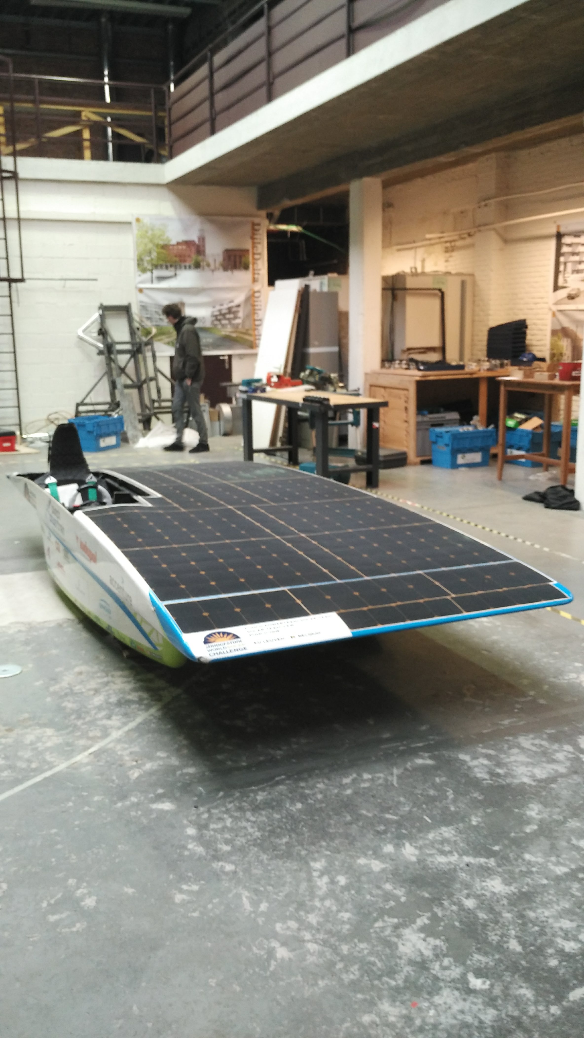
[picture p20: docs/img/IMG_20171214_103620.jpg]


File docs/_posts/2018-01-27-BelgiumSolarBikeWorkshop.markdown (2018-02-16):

---
layout: post
title: "Freedriving - Belgium Solar Bike Workshop "
date: 2018-01-27
background: "/img/IMG_20180127_102450.jpg"
---

We decided to cycle to Mechelen where Raf Van Hulle was organising a workshop
about the Sun Trip.  With an early start we were on the road by 6:45 AM.  It
was still dark outside when we rode along the Schelde eastbound.  Gradually the
clouded sky lighted up as we approached Dendermonde where we had a quick
pitstop at the LIDL.

From thereon out Auguste, sitting at the back, took on navigator duty and
guided us through the countryside towards Mechelen.  We were running slightly
late and after a short detour involving roadworks and passing a bakery to buy
lunch we arrived at Raf's place shortly after 10.

There we met the other Belgian particpants and sympathizers.  The info sessions
of Raf and Florian, one of the Sun Trip organisers, were very informative.  The
day quickly passed and at 6:30 PM we packed up and started our journey home.
It was already dark and a strong headwind made things harder.  To make things
worse it started raining, limiting visibility on the unlit path along the
Schelde.  Due to the lack of a rear fender Auguste's back and behind were being
showered with the cold water.

As we passed Wetteren disaster struck as Auguste sugar levels dropped and his
legs turned into spaghetti.  Luckily we quickly found a night shop and he
smashed a pint of Ben & Jerry's as we put in the final kilometers towards
Ghent.  Wet and tired we were happy to finally be home again around 10 PM.

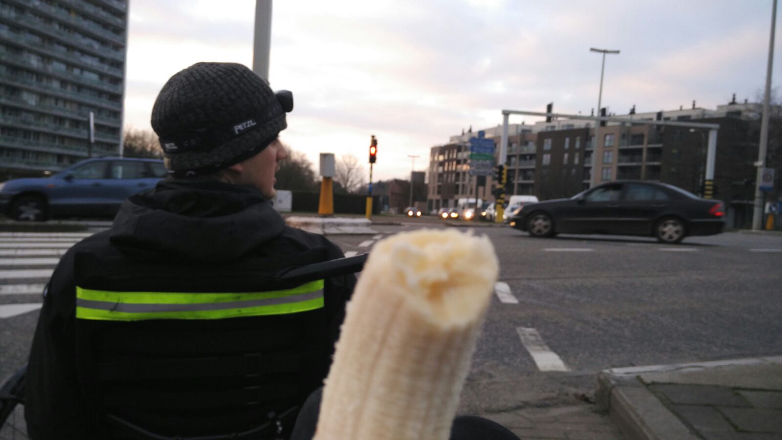
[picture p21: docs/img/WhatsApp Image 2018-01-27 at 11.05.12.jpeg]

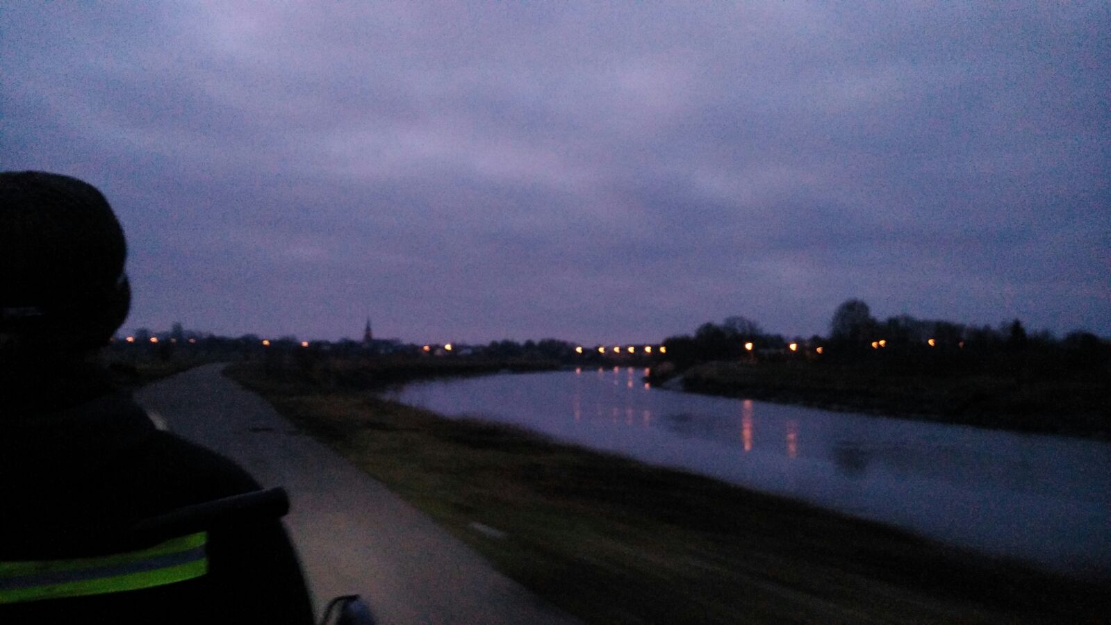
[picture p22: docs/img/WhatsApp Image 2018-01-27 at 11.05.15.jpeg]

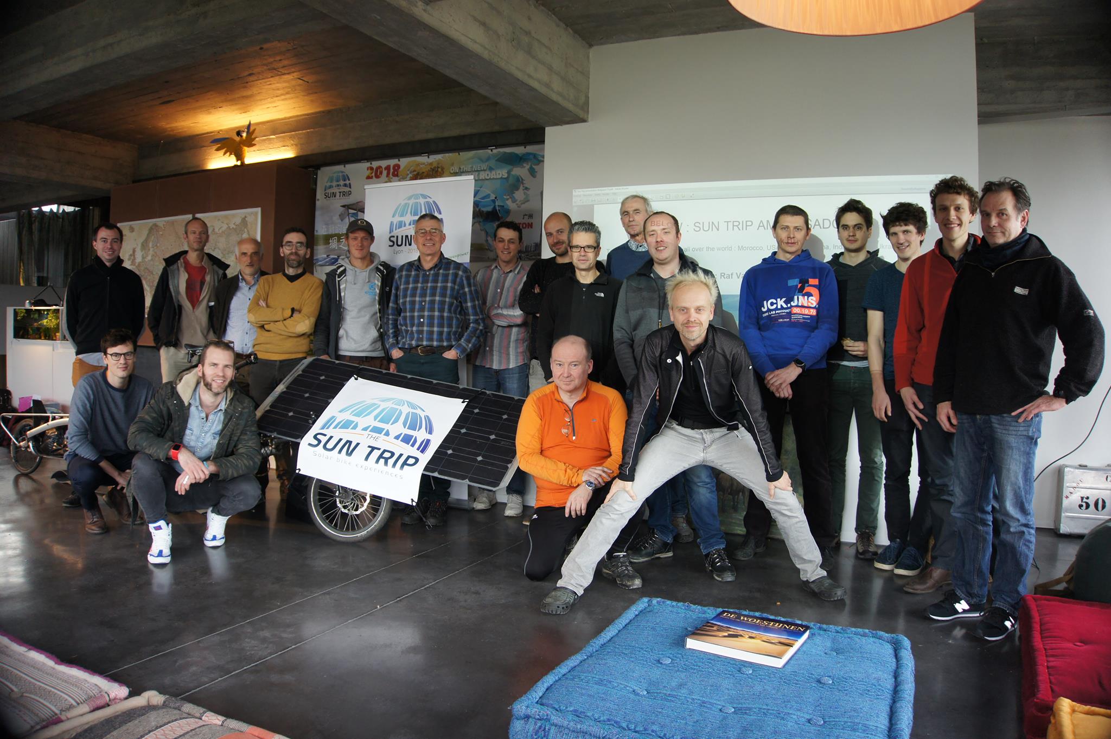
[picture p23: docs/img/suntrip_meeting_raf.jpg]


<iframe height='405' width='100%' frameborder='0' allowtransparency='true' scrolling='no' src='https://www.strava.com/activities/1377152431/embed/fa3d2d04b7d1c6246d4871ef8aabd0d5e6ac4265'></iframe>

<iframe height='405' width='100%' frameborder='0' allowtransparency='true' scrolling='no' src='https://www.strava.com/activities/1378419345/embed/db843fdfa6ab209bc6f2961bcc9d01aaf8cf95bf'></iframe>

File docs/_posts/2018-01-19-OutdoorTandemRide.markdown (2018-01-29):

---
layout: post
title: "Outdoor tandem ride"
date: 2018-01-19
background: "/img/WhatsApp Image 2018-01-19 at 17.15.46.jpeg"
---

Finally the sun has decided to come out again.  Although still a bit chilly we
set out in a decent headwind along the Leie towards Kortrijk.  In Deinze we had
to carry our tandem trike accross some roadworks.  We kept riding towards the
low-hanging sun, giving us some welcome sunshine on our faces, up to about 15
km out of Kortrijk where we turned around.

With the headwind turned into a tailwind and spotting a cyclist on the horizon,
destined to be overtaken by us we where blazing back north.  Auguste decided to
ignore his growing thirst in favor of keeping up the swift pace as we passed
Deinze.

Just as the sun was setting we rolled back into Ghent.

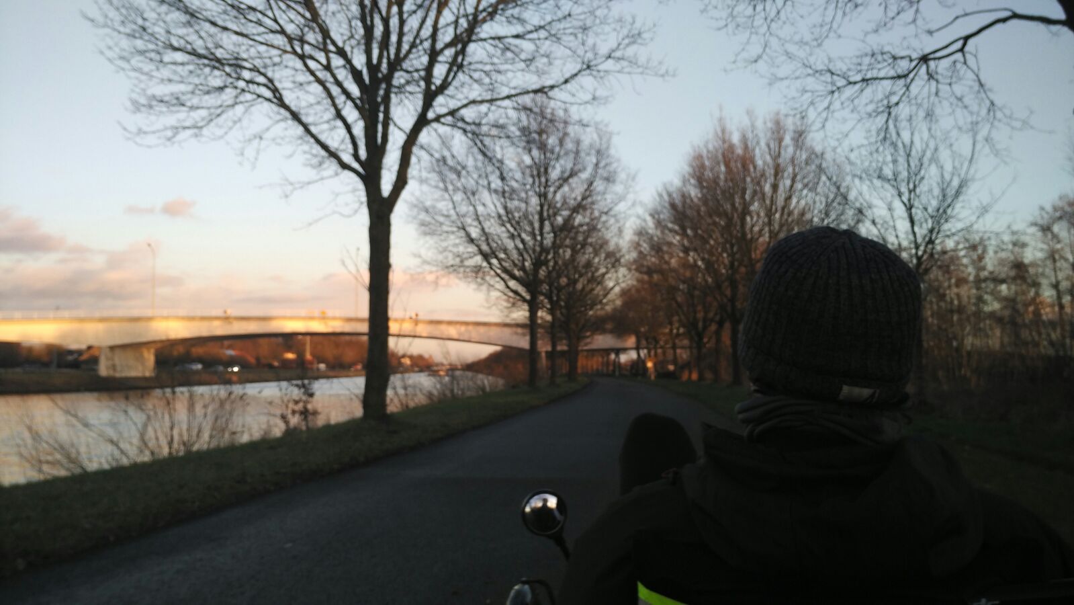
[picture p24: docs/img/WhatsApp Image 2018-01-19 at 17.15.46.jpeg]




<iframe height='405' width='100%' frameborder='0' allowtransparency='true' scrolling='no' src='https://www.strava.com/activities/1364739480/embed/960486c0d8b628c083841210d7c7b6ea5f8cc4b0'></iframe>

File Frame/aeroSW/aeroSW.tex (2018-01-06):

\documentclass[11pt]{article}

\usepackage{graphicx}
\usepackage{amssymb}
\usepackage{amsfonts}
\usepackage{amsmath}

\setlength{\parindent}{0pt}

\begin{document}

\section*{Aerodynamic simulation in SolidWorks Flow dink}

Solidworks flow simulation for a simplified version of the tandem trike (simple wheels, no chairs).
Increased ``global initial mesh refinement'' until results converge.

It is clear that predicted force $F$, and power $P$ calculated by $P = F v$ is low by a factor $\approx 3$. 

\begin{table}[h!]
\centering
\begin{tabular}{ | l | r | }
\hline
  & Drag (N) \\ \hline
 no roof & 15.9   \\
 flat roof & 17.0 \\
 curved roof & 19.1 \\
 curved roof and sidefenders & 18.5 \\
 covered front & 34.3 \\
 covered front and sidefenders & 30.6 \\
 curved front to ground & 72.1 \\  
 curved front to ground with plate & 61.2 \\ \hline
\end{tabular}
\caption{Drag force for wind speed of 10m/s, for different roof shapes}
\end{table}

\begin{figure}[h!]
\centering

\end{figure}

\begin{figure}[h!]
\centering

\end{figure}

\section*{Sideview velocity contour plots}

\begin{figure}

\caption{$v = 1 m/s$, global initial mesh = 2}
\end{figure}

\begin{figure}

\caption{$v = 1 m/s$, global initial mesh = 3}
\end{figure}

\begin{figure}

\caption{$v = 1 m/s$, global initial mesh = 4}
\end{figure}

\begin{figure}

\caption{$v = 1 m/s$, global initial mesh = 5}
\end{figure}

\begin{figure}

\caption{$v = 5 m/s$, global initial mesh = 2}
\end{figure}

\begin{figure}

\caption{$v = 5 m/s$, global initial mesh = 3}
\end{figure}

\begin{figure}

\caption{$v = 5 m/s$, global initial mesh = 4}
\end{figure}

\begin{figure}

\caption{$v = 5 m/s$, global initial mesh = 5}
\end{figure}

\begin{figure}

\caption{$v = 10 m/s$, global initial mesh = 2}
\end{figure}

\begin{figure}

\caption{$v = 10 m/s$, global initial mesh = 3}
\end{figure}

\begin{figure}

\caption{$v = 10 m/s$, global initial mesh = 4}
\end{figure}

\begin{figure}

\caption{$v = 10 m/s$, global initial mesh = 5}
\end{figure}

\clearpage

\section{roof tests}

\begin{figure}[ht]

\caption{$v = 10 m/s$, global initial mesh = 5. Note that with the roof the drag increases from 15N to 17N. }
\end{figure}

\begin{figure}[ht]

\caption{$v = 5 m/s$, global initial mesh = 5. Note that with the roof the drag increases from 4N to 5N but turbulent tail is significantly suppressed.}
\end{figure}

\begin{figure}[ht]

\caption{$v = 10 m/s$, global initial mesh = 5. Note that with the roof the drag increases from 15N to 19N but turbulent tail is significantly suppressed.}
\end{figure}

\begin{figure}[ht]
  
  \caption{roof and sidefender}
\end{figure}

\begin{figure}[ht]

\caption{$v = 10 m/s$, global initial mesh = 5. Adding sidefenders reduces drag force from 19N to 18.5N}
\end{figure}

\begin{figure}[ht]
  
  \caption{roof and sidefender}
\end{figure}

\begin{figure}[ht]

\caption{$v = 10 m/s$, global initial mesh = 5. Drag force is 34N}
\end{figure}

\begin{figure}[ht]
  
  \caption{roof and sidefender}
\end{figure}

\begin{figure}[ht]

\caption{$v = 10 m/s$, global initial mesh = 5. Adding sidefenders reduces drag from 34N to 30N.}
\end{figure}

\begin{figure}[ht]

\caption{$v = 10 m/s$, global initial mesh = 5. Drag is 72.1N.}
\end{figure}

\begin{figure}[ht]

\caption{$v = 10 m/s$, global initial mesh = 5. Drag reduces from 72.1N to 61.2N when adding bottom plate.}
\end{figure}

\end{document}

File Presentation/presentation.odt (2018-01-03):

Auguste & Camille Colle with KU Leuven

Two brothers, an industrial engineer and a theoretical physicist sharing a passion for cycling and ice cream. They ride under the banner of KU Leuven where Auguste is employed. The KU Leuven has participated in the Sun Trip 2016. Camille cycled 3 months trough the USA in the summer of 2017 and picked up a passion for long distance touring.

Instutional partner

KU Leuven is an institution for research and education with international appeal. All programmes at this University are based on the innovative research of its scientists and professors. The Energy & Automation (E&A) research group is one of the 14 research groups of the faculty of industrial engineering at the KU Leuven Technology Campus Ghent. The group is part of the ESAT cluster Electrical Engineering

The research of E&A is situated in the field of electrical energy technology and industrial automation. Various research projects led to the development of expertise in autonomous hybrid energy systems, industrial datacom and security, PV metrology, industrial energy measurements and light electrical mobility.

https://www.kuleuven.be

Sponsors

Trident Trikes is located in beautiful Lincolnton NC- about 45 miles NW of Charlotte. It is a small company, but it strives to be the best in design, innovation, and value in the Recumbent Trike industry, at the same time giving the best in personal customer service.

http://tridenttrikes.com/

(https://us.sunpower.com/)

Heliostream

http://www.heliostream.be/


Solar bicycle

The Chameleon tandem trike from tridenttrikes is converted to an electric assisted trike and fitted with solar panels from SunPower. In the design process both efficiency and robustness are investigated in detail.


Some words of the adventurers

Auguste: Nowadays most people agree that renewable energy and energy efficiency are of major concern. This explains shifts in consumer goods and government regulations, for example the subsidizing of photo-voltaic installations or the banning of halogen spotlights from the European market. With this in mind, how can one explain that most people still believe a 1500 kilogram vehicle is the normal way to go for transporting a 80 kg person? It's intriguing how the automobile sector dominates the main idea on how to get from one place to another. For this (and many other reasons) I really like the Sun Trip initiative, putting Light Electric Vehicles on the radar by demonstrating how much is possible with so much less. I'm looking forward to meet our fellow enthusiasts, to share ideas and to experience for myself that the average amateur solar bicycle beats the average industrial alternative on energy efficiency.

Camille: In march 2017 I finished my PhD in theoretical nuclear physics and took a much needed vacation. I decided to ride across the USA on my bicycle. The experience was unforgettable and resulted in a strong passion for cycling and long distance touring. Not long after I returned from my 3 month cycling adventure I started dreaming about a next long distance tour. When the opportunity arose to participate in the SunTrip with my brother under the banner of the KU Leuven, where he works, I didn’t hesitate for a second. The foresight of cycling all the way to China greatly entices me and I am looking forward to embark on this epic adventure. Additionally I think renewable energy and sustainability should be among the top-priorities in a modern society and I am happy to help advocate this view by participating in the sun trip.

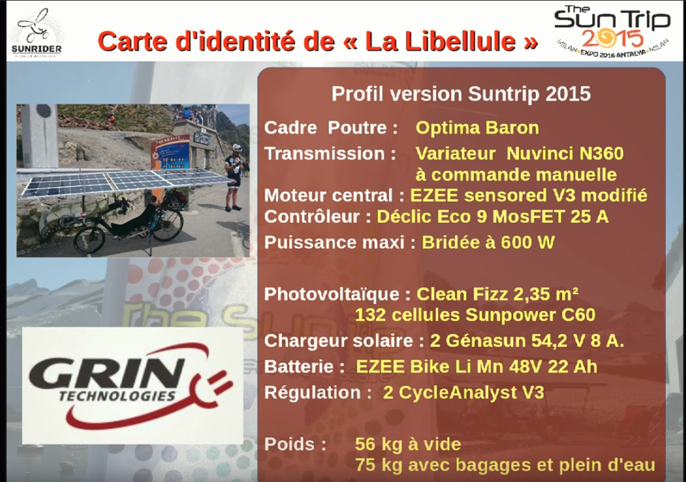
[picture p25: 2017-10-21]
Competition/images/bernard_cauquil-2015-specs.png

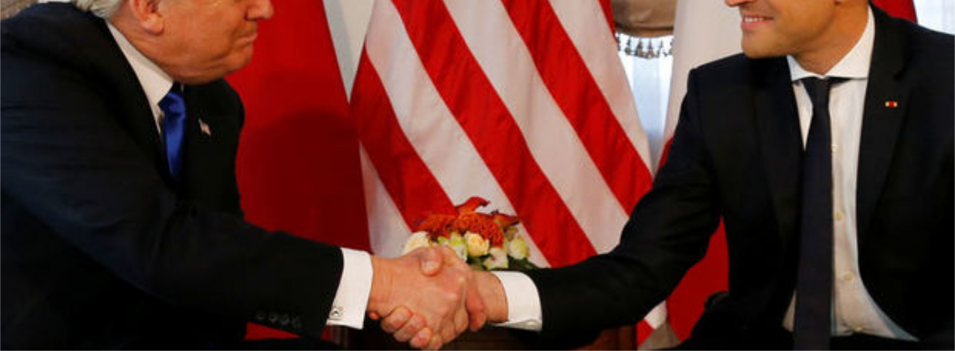
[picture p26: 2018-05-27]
docs/img/sponsors.png

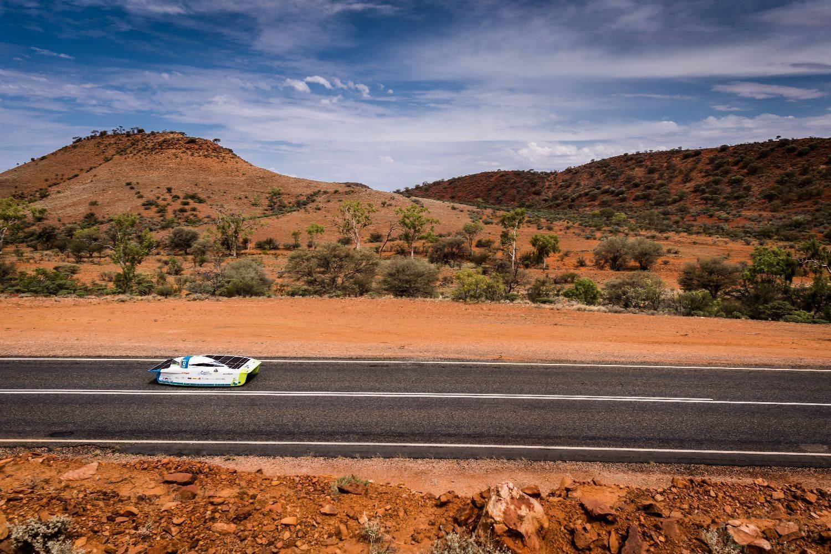
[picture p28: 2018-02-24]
docs/img/solar1.jpg

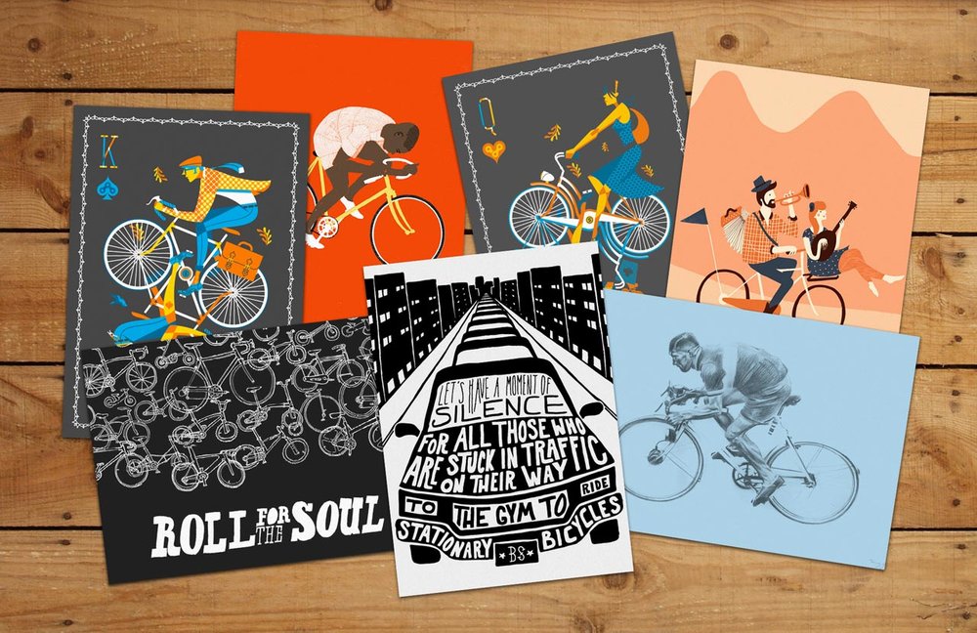
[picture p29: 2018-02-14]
docs/img/bicycle_postcards.jpg

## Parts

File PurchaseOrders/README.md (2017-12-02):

Purchase Orders
===============

Here all current Purchase Orders are listed and the TO ORDER list is being monitored by Auguste, he will order parts on the list as soon as possible. Normal workflow:

TO ORDER -> Purchase Order -> Invoice -> Notification when the goods arrive

For the notification it is necessary that the name (or emoji) of the person who added something on the TO ORDER list is displayed. For example:

1. [Eno-freewheel](http://sickbikeparts.com/front-freewheel-heavy-duty/), quantity 4, :hear_no_evil:

TO ORDER:
---------

:smirk_cat: ** Bikester **
- ~~[8 speed shimano cassette](https://www.bikester.be/fietsonderdelen/fietsketting-cassette/cassette-6-7-8-voudig/335180.html), quantity 1~~ DONE :hear_no_evil:
- ~~[8 speed derailleur](https://www.bikester.be/shimano-altus-rd-m310-achterderailleur-7-8-fach-kurz-zwart-707645.html), quantity 1~~ DONE :hear_no_evil:
- ~~[tandem shifter cable](https://www.bikester.be/shimano-tandem-stainless-schakelkabel-12x3000mm-zilver-695544.html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), quantity 2~~ DONE :hear_no_evil:
- ~~[8 speed chain](https://www.bikester.be/fietsonderdelen/fiets-cassettes-fietskettingen/678-speed-kettingen/224138.html), quantity 2~~ DONE :hear_no_evil:
- ~~[velglint](https://www.bikester.be/schwalbe-tubeless-velglint-10m-x-25mm-blauw-401944.html), quantity 1~~ DONE :hear_no_evil: NOTE: I changed this to a non-tubeless version. I chose 15mm width since this is the closest match (available on bikester) with the rim of 14mm.

:smirk_cat: ** Bikester **
- [9 speed shimano casette](https://www.bikester.be/shimano-cs-hg201-cassette-9s-zilver-644108.html)
- [9 speed chain](https://www.bikester.be/shimano-deore-cn-hg53-fietsketting-9-speed-grijs-551920.html)
- [centerlock disk brake](#) Measure existing rotors first for correct diameter!
- [handlebar grips](#) measure needed length/width?

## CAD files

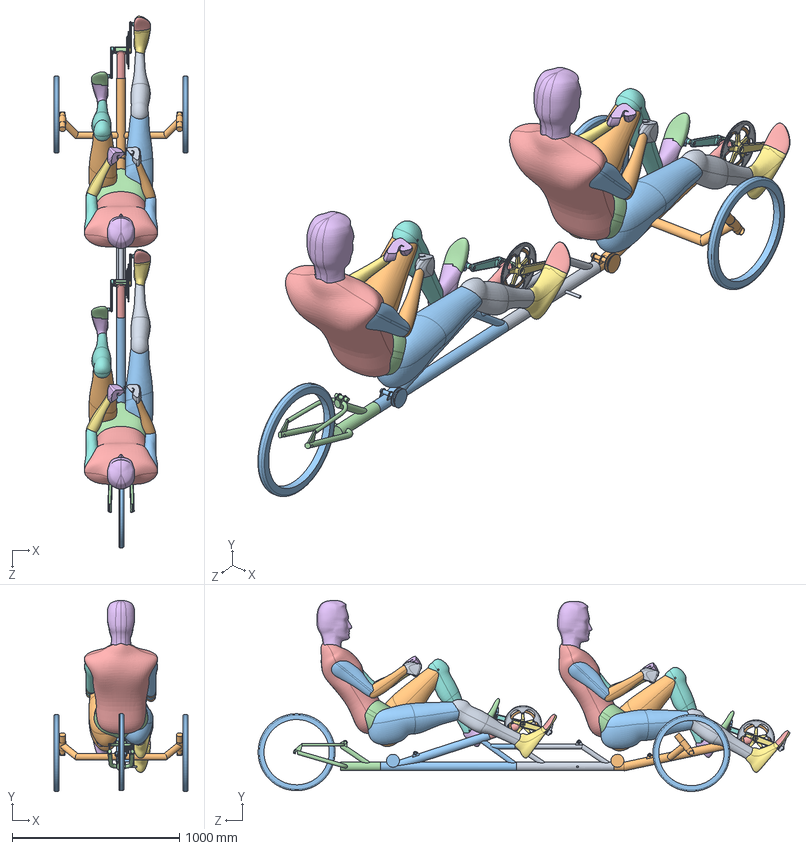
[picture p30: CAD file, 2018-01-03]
Frame/Solidworks/Assembly/Assembly_simple.SLDASM
800.4 x 1141.2 x 3176.9 mm
Part2_new
buis_voor_trappers x 2
l_hand x 2
l_forearm x 2
l_uprarm x 2
r_hand x 2
r_forearm x 2
r_uprarm x 2
Mirrorr_toe x 2
r_toe x 2
Mirrorr_foot x 2
r_foot_new x 2
Mirrorr_calf_new x 2
r_calf_new x 2
Mirrorr_thigh x 2
r_thigh x 2
pelvis x 2
torso x 2
head x 2
pedal_axle x 4
pedal_nut x 4
pedal_body_r x 2
Angular Contact Ball Bearing_68_ISO x 8
pedal_body_l x 2
bb_shell x 2
bb_axle x 2
Angular Contact Ball Bearing_68_ISO_17X35X10_ISO 15 ABB - 1017 - 12,SI,NC,12_68 x 4
crankarm_r x 2
crankarm_l x 2
bigring_54 x 2
smallring_42 x 2
20 inch wheel simple x 3

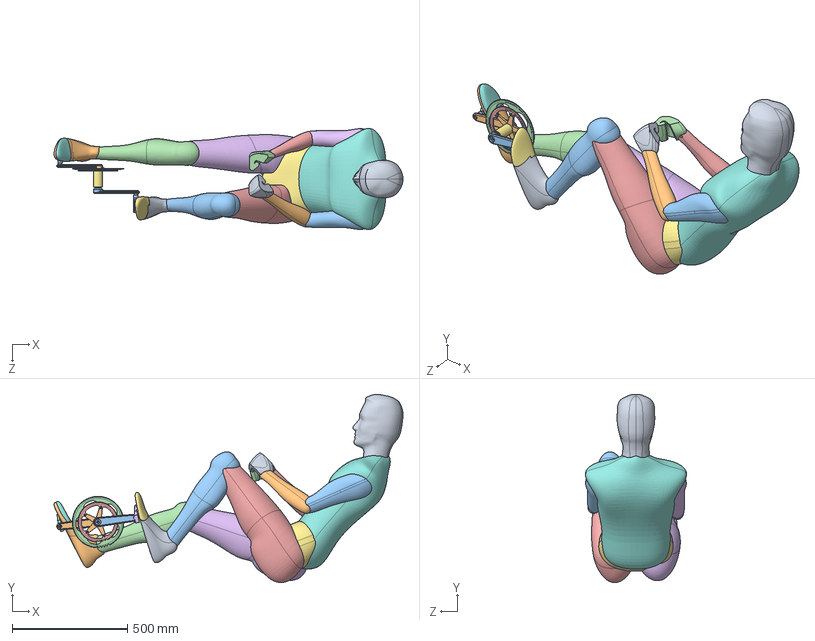
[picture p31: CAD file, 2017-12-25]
Frame/Solidworks/Assembly/man and pedals.SLDASM
1510.9 x 814.4 x 437.5 mm
l_hand
l_forearm
l_uprarm
r_hand
r_forearm
r_uprarm
Mirrorr_toe
r_toe
Mirrorr_foot
r_foot_new
Mirrorr_calf_new
r_calf_new
Mirrorr_thigh
r_thigh
pelvis
torso
head
pedal_axle x 2
pedal_nut x 2
pedal_body_r
Angular Contact Ball Bearing_68_ISO x 4
pedal_body_l
bb_shell
bb_axle
Angular Contact Ball Bearing_68_ISO_17X35X10_ISO 15 ABB - 1017 - 12,SI,NC,12_68 x 2
crankarm_r
crankarm_l
bigring_54
smallring_42

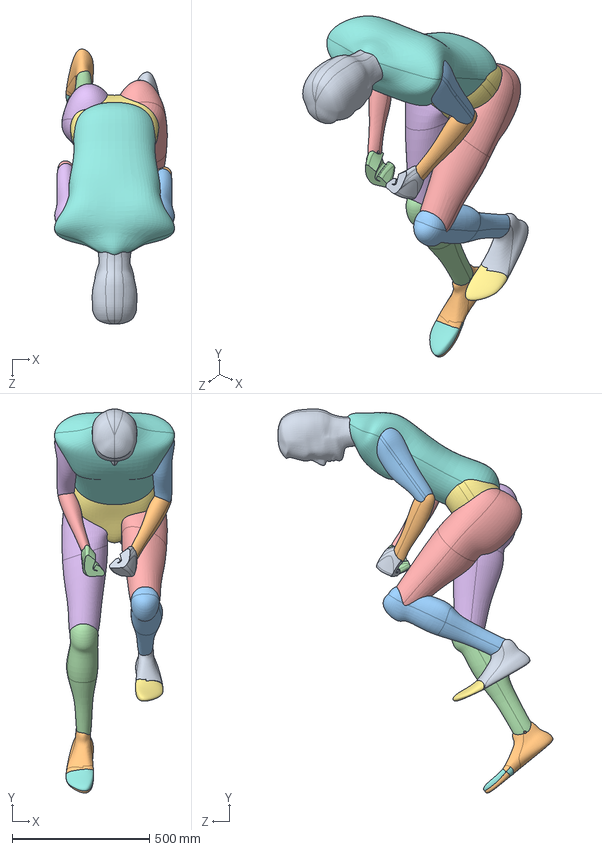
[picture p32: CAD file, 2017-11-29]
Frame/Solidworks/Assembly/man.sldasm
437.5 x 1399.9 x 1002.3 mm
l_hand
l_forearm
l_uprarm
r_hand
r_forearm
r_uprarm
Mirrorr_toe
r_toe
Mirrorr_foot
r_foot_new
Mirrorr_calf_new
r_calf_new
Mirrorr_thigh
r_thigh
pelvis
torso
head

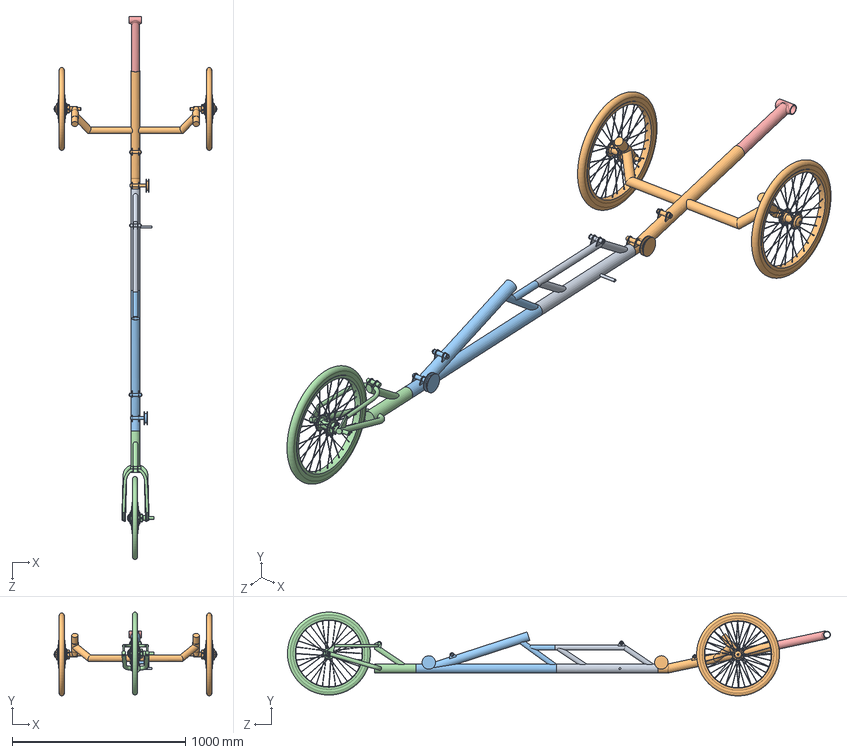
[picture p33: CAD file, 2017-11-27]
Frame/Solidworks/Assembly/Assembly.SLDASM
938.0 x 483.4 x 3131.4 mm
Part2_new
buis_voor_trappers

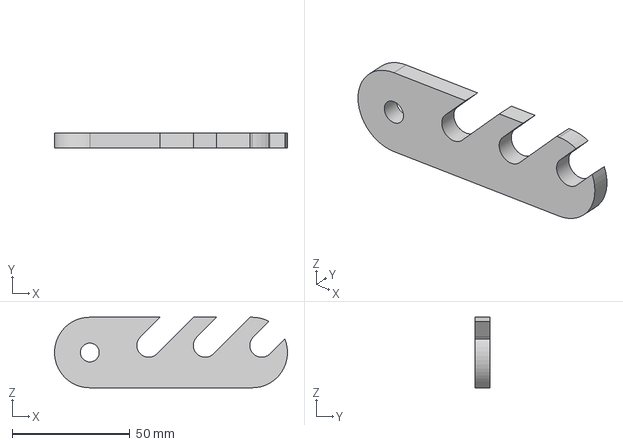
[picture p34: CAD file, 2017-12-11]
Frame/Klemmen/SpacersZitjeAchter v2.step
99.0 x 6.50 x 30.0 mm

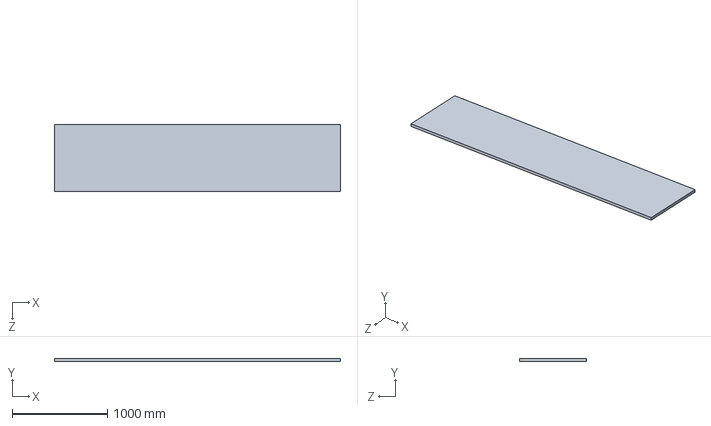
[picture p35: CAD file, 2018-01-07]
Frame/Solidworks/Assembly/roof_test0.SLDPRT
3000.0 x 30.0 x 700.0 mm

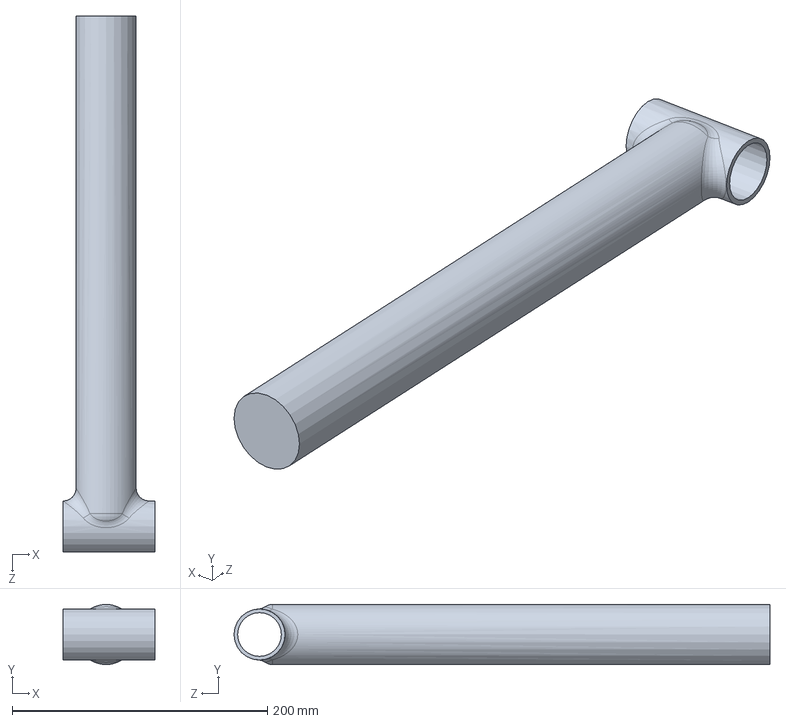
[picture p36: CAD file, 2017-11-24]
Frame/Solidworks/Part1/buis_voor_trappers.SLDPRT
72.3 x 47.1 x 420.0 mm

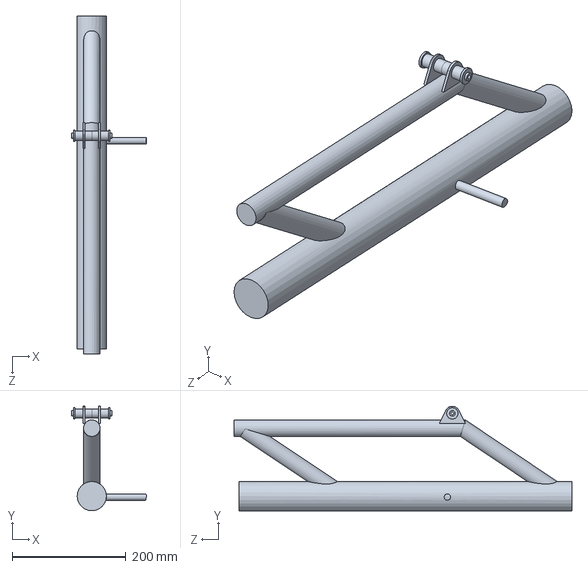
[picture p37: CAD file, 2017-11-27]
Frame/Solidworks/Part2/Part2_new.SLDPRT
131.0 x 183.4 x 593.2 mm

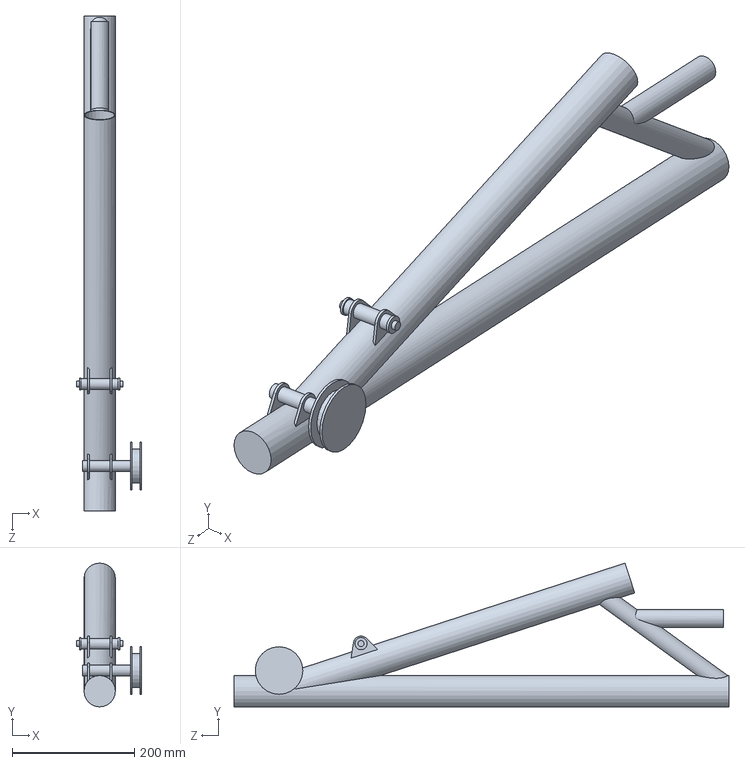
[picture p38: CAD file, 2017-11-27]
Frame/Solidworks/Part3/Part3.SLDPRT
107.1 x 235.6 x 811.0 mm

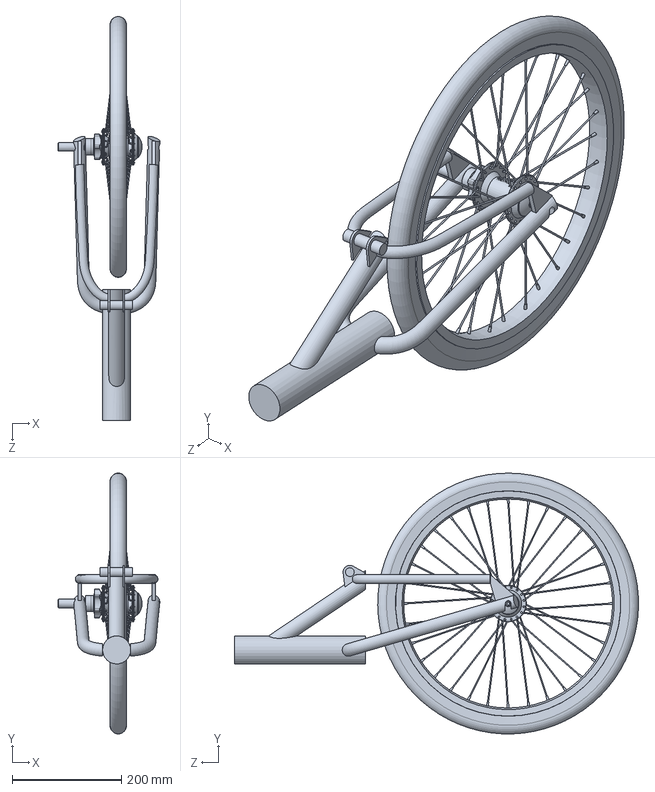
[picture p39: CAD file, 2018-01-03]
Frame/Solidworks/Part4/Part4.SLDPRT
186.7 x 478.4 x 741.1 mm

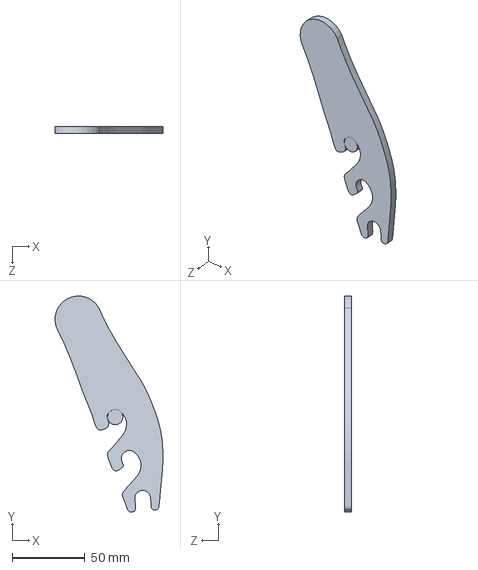
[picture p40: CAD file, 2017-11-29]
Frame/Solidworks/Part5/steun_onder.SLDPRT
74.4 x 148.8 x 5.00 mm

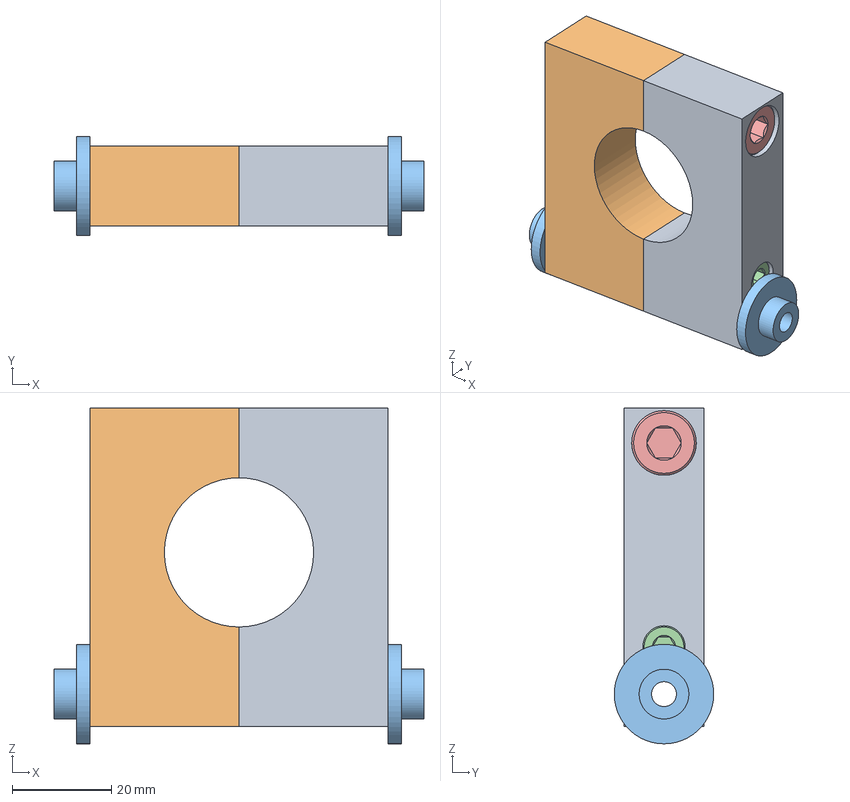
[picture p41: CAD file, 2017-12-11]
Frame/Klemmen/KlemZitjeVooraan-achterkant v2.step
74.4 x 20.0 x 67.5 mm
91290A262
91290A448

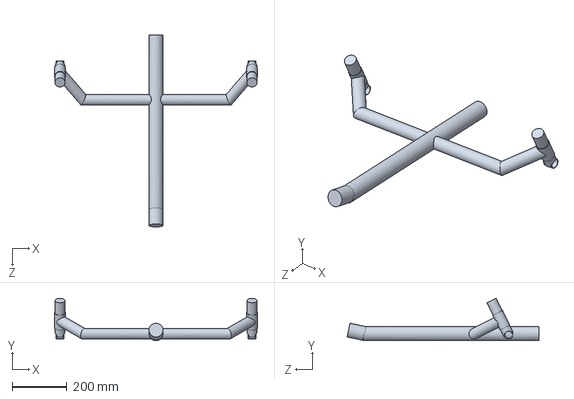
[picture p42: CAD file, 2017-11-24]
Frame/Solidworks/Part1/Part1.SLDPRT
740.0 x 154.6 x 699.4 mm

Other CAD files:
Frame/Solidworks/Assembly/pedal_l_asm.sldasm
Frame/Solidworks/Assembly/pedal_r_asm.sldasm
Frame/Solidworks/Assembly/crank bb and pedals 68mm.sldasm
Frame/Solidworks/Assembly/bb.sldasm
Frame/Solidworks/Assembly/staart_v1.SLDPRT
Frame/Klemmen/KlemZitjeVooraan-eenvoudig v4.step
Frame/Solidworks/Assembly/20 inch wheel simple.SLDPRT
Frame/Solidworks/Assembly/20 inch wheel.SLDPRT
Frame/Solidworks/Assembly/Angular Contact Ball Bearing_68_ISO.sldprt
Frame/Solidworks/Assembly/Angular Contact Ball Bearing_68_ISO_17X35X10_ISO 15 ABB - 1017 - 12,SI,NC,12_68.sldprt
Frame/Solidworks/Assembly/Mirrorr_calf_new.sldprt
Frame/Solidworks/Assembly/Mirrorr_foot.sldprt
Frame/Solidworks/Assembly/Mirrorr_thigh.sldprt
Frame/Solidworks/Assembly/Mirrorr_toe.sldprt
Frame/Solidworks/Assembly/Mirrorsidefender.SLDPRT
Frame/Solidworks/Assembly/assembly_KUL.SLDDRW
Frame/Solidworks/Assembly/bb_axle.sldprt
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

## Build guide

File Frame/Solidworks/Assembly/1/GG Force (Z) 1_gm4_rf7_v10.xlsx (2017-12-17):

GG Force (Z) 1
Iterations [ ] | Force (Z) [N]
1 | 552.4926391
2 | 134.0615479
3 | 73.72773384
4 | 41.13551142
5 | 45.00206317
6 | 37.1050932
7 | 37.78142708
8 | 34.17123773
9 | 34.32688727
10 | 32.50629075
11 | 32.72113706
12 | 32.03126633
13 | 31.78201032
14 | 31.06045944
15 | 30.62266972
16 | 29.7671
17 | 28.81016155
18 | 27.7619597
19 | 26.88449855
20 | 26.09232243
21 | 25.39679448
22 | 24.50469008
23 | 23.78039836
24 | 23.20006917
25 | 22.7206986
26 | 22.33655291
27 | 21.85462089
28 | 21.46145584
29 | 21.13952351
30 | 20.85156467
31 | 20.58744949
32 | 20.26098474
33 | 20.00693744
34 | 19.72395498
35 | 19.51900695
36 | 19.32326652
37 | 19.15436142
38 | 18.97142173
39 | 18.82886016
40 | 18.68358438
41 | 18.58069796
42 | 18.43036438
43 | 18.30089938
44 | 18.13667153
45 | 18.03658063
46 | 17.8970135
47 | 17.78816501
48 | 17.65845507
49 | 17.55820991
50 | 17.42691617
51 | 17.32278445
52 | 17.19594355
53 | 17.11220675
54 | 16.99089826
55 | 16.88587701
56 | 16.77057912
57 | 16.67101451
58 | 16.54552809
59 | 16.44239478
60 | 16.32579777
61 | 16.25359223
62 | 16.16093163
63 | 16.07390954
64 | 15.97695371
65 | 15.89508058
66 | 15.79992878
67 | 15.71184619
68 | 15.62789326
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

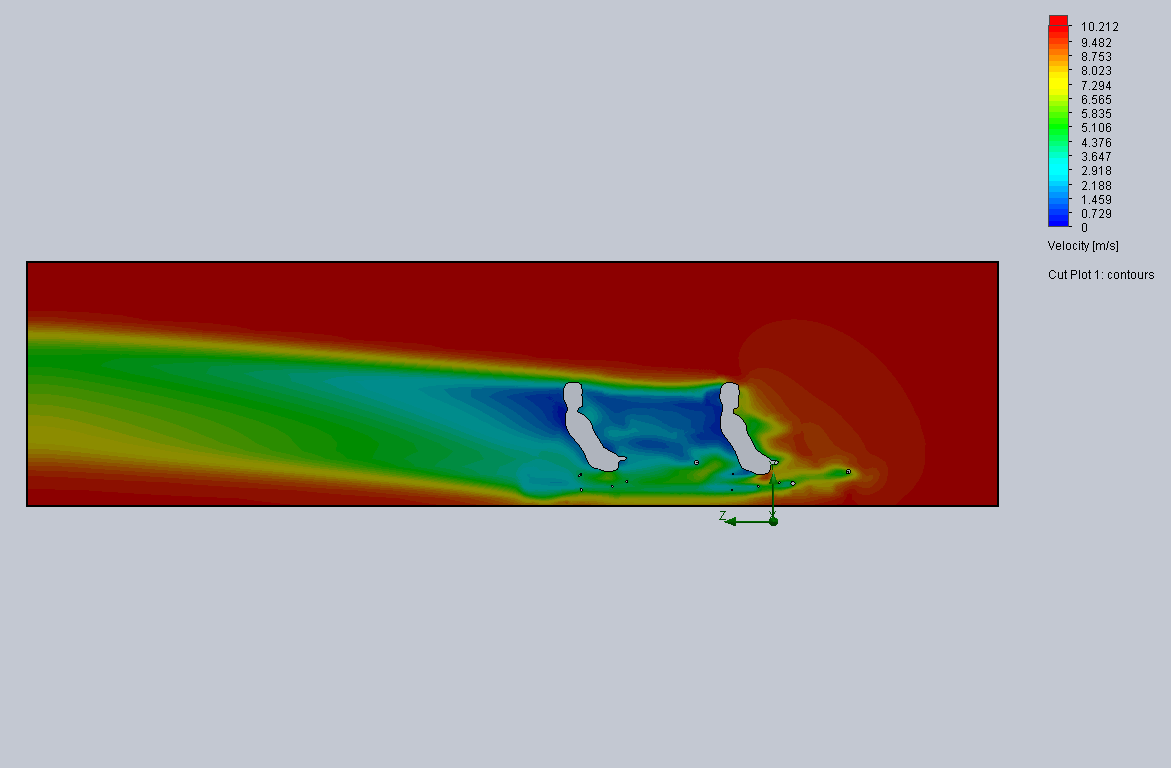
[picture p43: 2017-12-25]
Frame/Solidworks/Assembly/1/gm_5_rf_7_v10_sidefender.png

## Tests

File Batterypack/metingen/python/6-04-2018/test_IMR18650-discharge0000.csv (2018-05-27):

Tijd | Spanning | Stroom
10:01:44 | 0.024844 | -2.2e-05
10:01:45 | 0.024269 | -1.7e-05
10:01:46 | 0.025255 | -4.9e-05
10:01:47 | 0.024466 | -1.1e-05
10:01:48 | 0.025386 | -4e-05
10:01:49 | 0.025666 | -4e-05
10:01:50 | 0.025755 | -8e-06
10:01:51 | 0.024933 | -3.7e-05
10:01:52 | 0.025085 | -8e-06
10:01:53 | 4.177171 | 1e-05
10:01:54 | 4.177144 | -6.7e-05
10:01:55 | 4.177112 | 1.3e-05
10:01:56 | 4.177076 | -1.1e-05
10:01:57 | 4.177046 | 4e-06
10:01:58 | 4.177013 | -2e-06
10:01:59 | 4.176978 | -8e-06
10:02:00 | 4.170841 | 0.163337
10:02:01 | 4.143198 | 0.376503
10:02:02 | 4.124187 | 0.661846
10:02:03 | 4.104955 | 0.760716
10:02:04 | 4.103687 | 0.76128
10:02:05 | 4.102666 | 0.762089
10:02:06 | 4.101799 | 0.763033
10:02:07 | 4.10101 | 0.76463
10:02:08 | 4.100206 | 0.763783
10:02:09 | 4.099787 | 0.763771
10:02:10 | 4.098977 | 0.765076
10:02:11 | 4.098372 | 0.764934
10:02:12 | 4.097661 | 0.766094
10:02:13 | 4.097199 | 0.766732
10:02:14 | 4.096547 | 0.767083
10:02:15 | 4.096059 | 0.766634
10:02:16 | 4.09541 | 0.768178
10:02:17 | 4.094969 | 0.769173
10:02:18 | 4.094588 | 0.768533
10:02:19 | 4.094165 | 0.769397
10:02:20 | 4.093561 | 0.771036
10:02:21 | 4.093072 | 0.769628
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

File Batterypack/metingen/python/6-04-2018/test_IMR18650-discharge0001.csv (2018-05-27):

Tijd | Spanning | Stroom
10:18:25 | 3.892522 | 1.004904
10:18:26 | 3.892271 | 1.004797
10:18:27 | 3.892221 | 1.005072
10:18:28 | 3.892087 | 1.004827
10:18:29 | 3.89189 | 1.00609
10:18:30 | 3.89178 | 1.004434
10:18:31 | 3.89139 | 1.007179
10:18:32 | 3.891387 | 1.007165
10:18:33 | 3.891131 | 1.007551
10:18:34 | 3.891077 | 1.007888
10:18:35 | 3.890759 | 1.008617
10:18:36 | 3.890539 | 1.007737
10:18:37 | 3.890419 | 1.008044
10:18:38 | 3.89041 | 1.008895
10:18:39 | 3.890131 | 1.007723
10:18:40 | 3.890065 | 1.008272
10:18:41 | 3.889818 | 1.007991
10:18:42 | 3.889678 | 1.008945
10:18:43 | 3.889401 | 1.009278
10:18:44 | 3.889362 | 1.007734
10:18:45 | 3.889169 | 1.00769
10:18:46 | 3.889166 | 1.007115
10:18:47 | 3.889041 | 1.006509
10:18:48 | 3.888955 | 1.007596
10:18:49 | 3.888669 | 1.006881
10:18:50 | 3.888556 | 1.007188
10:18:51 | 3.888422 | 1.007386
10:18:52 | 3.888329 | 1.005258
10:18:53 | 3.888157 | 1.00648
10:18:54 | 3.888043 | 1.007377
10:18:55 | 3.887957 | 1.007239
10:18:56 | 3.887731 | 1.007489
10:18:57 | 3.88754 | 1.00645
10:18:58 | 3.887454 | 1.006489
10:18:59 | 3.887263 | 1.007191
10:19:00 | 3.887117 | 1.008729
10:19:01 | 3.886995 | 1.006802
10:19:02 | 3.886656 | 1.007714
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

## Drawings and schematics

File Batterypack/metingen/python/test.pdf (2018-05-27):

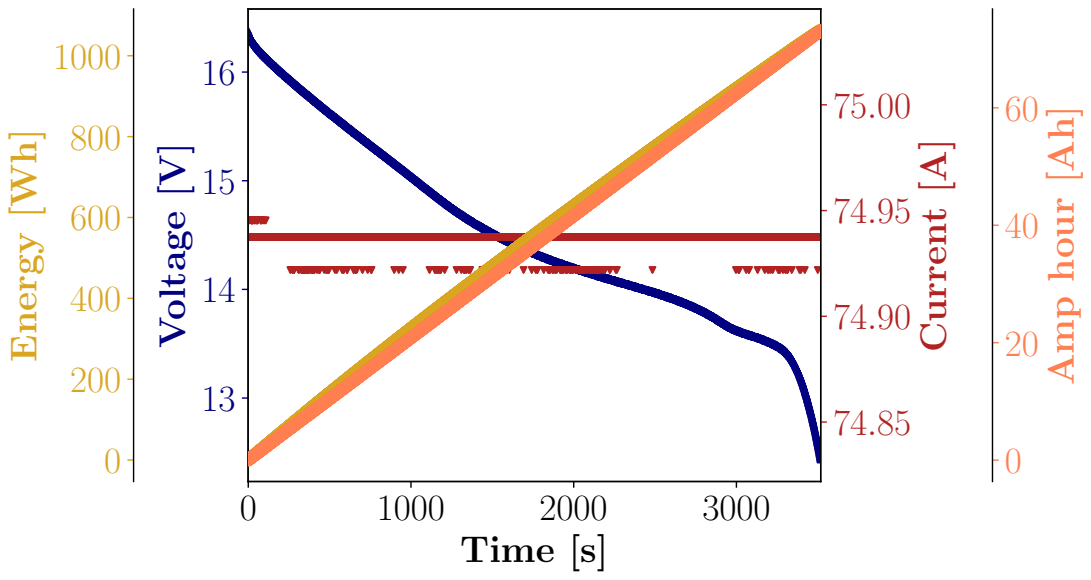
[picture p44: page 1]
Time [s]; Voltage [V]; Current [A]; Energy [Wh]

Amp hour [Ah]

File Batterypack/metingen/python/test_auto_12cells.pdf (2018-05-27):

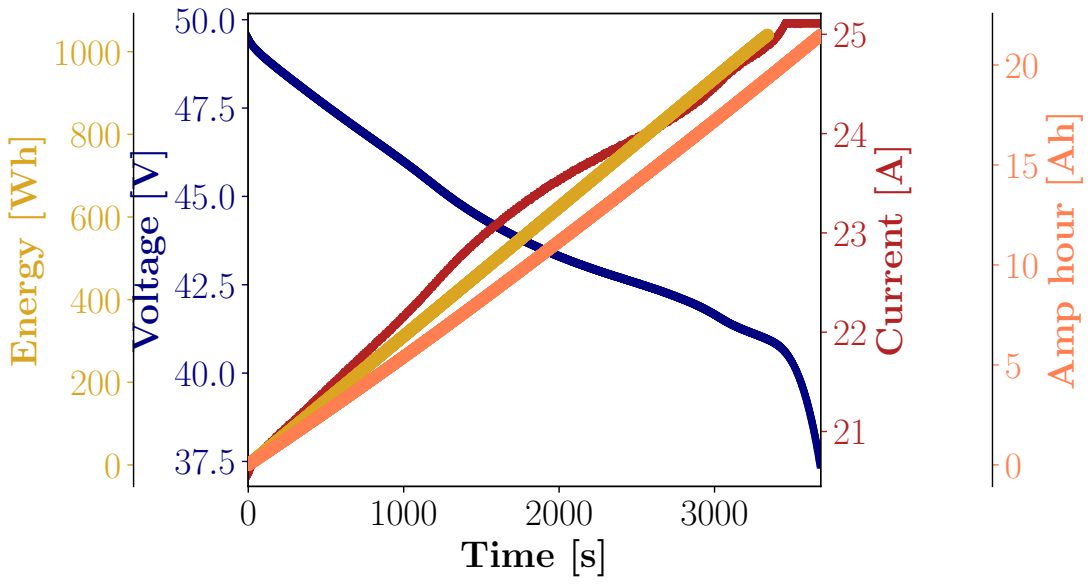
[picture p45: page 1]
Time [s]; Voltage [V]; Current [A]; Energy [Wh]

Amp hour [Ah]

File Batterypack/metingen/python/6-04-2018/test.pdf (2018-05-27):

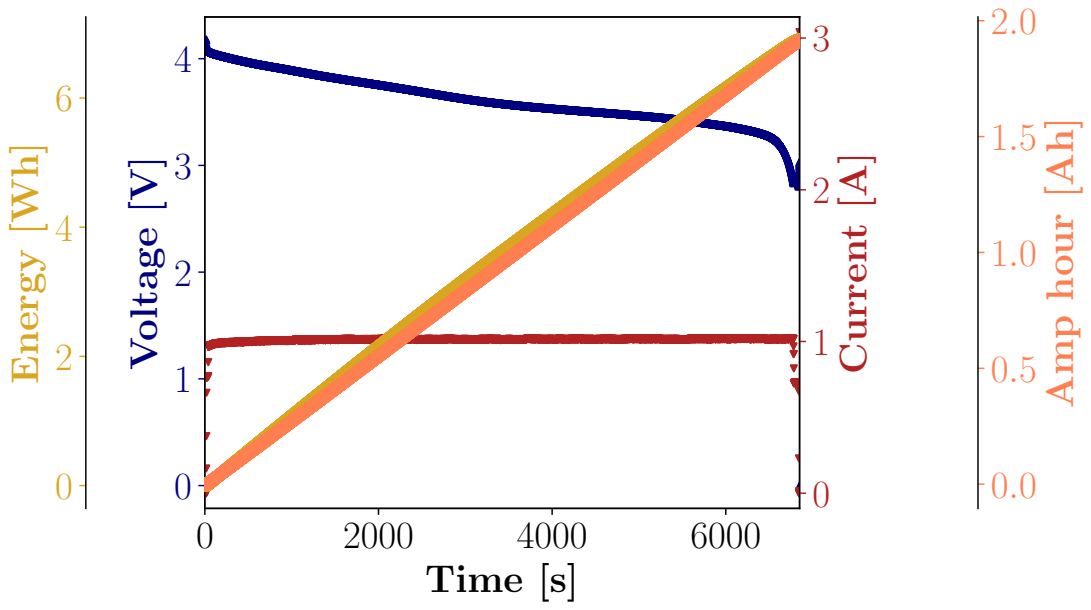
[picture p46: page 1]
Time [s]; Voltage [V]; Current [A]; Energy [Wh]

Amp hour [Ah]

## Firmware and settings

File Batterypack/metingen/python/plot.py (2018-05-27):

import glob
import os
import matplotlib.pyplot as plt
import numpy as np

numcells = 1.
dirname = "test_auto_12cells"


def setplotparams():
    ''' Set a bunch of plot paramaters '''
    plt.rcParams.update(plt.rcParamsDefault)
    params = {  # 'legend.fontsize':        27,
                # 'axes.linewidth':         3.5,
                # 'axes.labelsize':         25,
                # 'xtick.minor.size':       6,
                # 'xtick.minor.width':      2,
                # 'xtick.major.pad':        10,
                # 'xtick.major.width':      4,
                # 'xtick.major.size':       12,
                # 'ytick.minor.size':       6,
                # 'ytick.minor.width':      2,
                # 'ytick.major.width':      4,
                # 'ytick.major.size':       12,
                # 'xtick.labelsize':        20,
                # 'ytick.labelsize':        20,
              'errorbar.capsize':       4,
              'text.usetex':            True,
              'text.latex.preamble':    "\\usepackage{amsmath} \
                                         \\usepackage{amssymb} \
                                         \\usepackage{amsfonts}",
              'font.size':              21,
              'font.family':            'serif',
              'font.serif':             'Computer Modern'
              }
    plt.rcParams.update(params)


def make_patch_spines_invisible(ax):
    ax.set_frame_on(True)
    ax.patch.set_visible(False)
    for sp in ax.spines.values():
        sp.set_visible(False)


def getAllData(dir, suffix):
    '''Get the data from the .suffix files at path dir,
    returns the data from all .suffix files in dir.'''
    pwd = os.getcwd()
    os.chdir(dir)
    print(os.getcwd())
    time = [None]*10000
    voltage = [None]*10000
    current = [None]*10000
    count = 0
    files = glob.glob("*." + suffix)
    files.sort()
    for filename in files:
        print(filename)
        tempT, tempV, tempI = np.loadtxt(filename, skiprows=1, unpack=True,
                                         delimiter=',', usecols=(0, 1, 2),
                                         converters={0: lambda s: np.sum(
                                             [int(i)*y for i, y in zip(
                                                 s.decode().split(':'),
                                                 [3600, 60, 1])]
                                         )
                                                     })
        time[count:(count + len(tempV))] = tempT
        voltage[count:(count + len(tempV))] = tempV
        current[count:(count + len(tempV))] = tempI
        count += len(tempV)
    os.chdir(pwd)
    time[:count] = time[:count] - time[0]
    return time[:count], voltage[:count], current[:count]


def main():
    setplotparams()
    plt.clf()
    plt.cla()
    plt.close('all')
    fig, ax1 = plt.subplots()
    fig.subplots_adjust(left=0.15, right=0.85)
    secs, volts, amps = getAllData(dirname, "csv")
    ax1.scatter(secs, volts, color='navy', s=12., marker='^')
    #  ax1.errorbar(secs, volts, yerr=(80e-3), errorevery=100,
    #               ecolor='navy', fmt='none')
    ax1.set_xlabel(r"\textbf{Time [s]}")
    ax1.set_ylabel(r"\textbf{Voltage [V]}", color="navy")
    ax1.tick_params("y", colors="navy")
    ax1.set_xlim([secs[0]-1, secs[-1]+1])
    ax2 = ax1.twinx()
    ax2.scatter(secs, amps, color='firebrick', s=12., marker='v')
    #  ax2.errorbar(secs, amps, yerr=(2e-3*200), errorevery=100,
    #               ecolor='firebrick', fmt='none')
    ax2.set_ylim([np.min(amps)-.1, np.max(amps)+.1])
    ax2.set_ylabel(r"\textbf{Current [A]}", color="firebrick")
    ax2.tick_params('y', colors='firebrick')

    shifted = [0] + list(secs[:-1])
    secs_diff = secs - np.array(shifted)
    e = (np.array(volts)*np.array(amps)*secs_diff).cumsum()/3600.

    ax3 = ax1.twinx()
    # Offset the right spine of ax3.  The ticks and label have already been
    # placed on the right by twinx above.
    ax3.spines["left"].set_position(("axes", -0.2))
    # Having been created by twinx, ax3 has its frame off, so the line of its
    # detached spine is invisible.  First, activate the frame but make the patch
    # and spines invisible.
    ax3.yaxis.set_label_position('left')
    ax3.yaxis.set_ticks_position('left')
    make_patch_spines_invisible(ax3)
    # Second, show the right spine.
    ax3.spines["left"].set_visible(True)
    ax3.scatter(range(len(amps)), e/numcells, color='goldenrod')
    #  ax3.errorbar(range(len(amps)), e/numcells, yerr=[e_uerror/numcells,
    #                                                   e_lerror/numcells],
    #               color='goldenrod', fmt='none', errorevery=100, size=6.)
    ax3.set_ylabel(r"\textbf{Energy [Wh]}", color="goldenrod")
    ax3.tick_params("y", colors="goldenrod")

    ax4 = ax1.twinx()
    # Offset the right spine of ax3.  The ticks and label have already been
    # placed on the right by twinx above.
    ax4.spines["right"].set_position(("axes", 1.3))
    # Having been created by twinx, ax3 has its frame off, so the line of its
    # detached spine is invisible.  First, activate the frame but make the patch
    # and spines invisible.
    ax4.yaxis.set_label_position('right')
    ax4.yaxis.set_ticks_position('right')
    make_patch_spines_invisible(ax4)
    # Second, show the right spine.
    ax4.spines["right"].set_visible(True)
    amph = np.array(amps).cumsum()/(3600*numcells)
    ax4.scatter(secs, amph, color='coral')
    ax4.set_ylabel(r"\textbf{Amp hour [Ah]}", color="coral")
    ax4.tick_params("y", colors="coral")
    plt.savefig("test_auto_12cells.pdf", bbox_inches='tight')

    print("{:<30}{:>10.2f} Ah".format("Total amp hour: ", amph[-1]))
    print("{:<30}{:>10.2f} Wh".format("Total watt hour: ", e[-1]/numcells))


if __name__ == "__main__":
    main()

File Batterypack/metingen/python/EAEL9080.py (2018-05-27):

import serial as serial
import time
import binascii
import numpy as np

DevNode = "01" #device node, manual configured on machine, standard value is 01
pause = 0.01 #used for a timeout between sending command and reading buffer for the response
vNom = 80.0 #on machine, nominal votage
iNom = 200.0
pNom = 2400.0
rNom = 100


def startSerial(port = '/dev/ttyUSB0', devicenode = "02"):
    '''Initialize serial communication with the default values on page 28 of the programming manual. The devicenode (global DevNode, a two character string) is standard set to "01" but is device dependent, the port is standard set to /dev/ttyUSB0 cause this program was written on a linux distribution'''
    global DevNode
    global ser
    DevNode = devicenode
    ser = serial.Serial(port, baudrate=57600, parity=serial.PARITY_ODD, stopbits=serial.STOPBITS_ONE, timeout=0)
    return ser


def stopSerial():
    '''Stops serial communication'''
    global ser
    ser.close()
    return 0


def clearBuffer():
    ser.flushInput()
    ser.flushOutput()


def checksum(dataList):
    '''calculates checksum and returns it'''
    checksum = 0
    for hexVal in dataList:
        checksum += int(binascii.hexlify(hexVal).decode('UTF-8'), 16)
    checksum = hex(checksum)[2:].zfill(4)
    return bytes.fromhex(checksum)


def readAndTreat(maxbytes = 20):
    '''Reads and treats the incomming data. The default value for the maximum on incomming bytes is arbitrary set to 100, although not so arbitrary since I think a larger response from the device is not possible unless one forgets to read the buffer. Returns the treated data as an array of hex numbers'''
    time.sleep(0.05)
    inBuffer = ser.read(maxbytes)
    inBuffer = binascii.hexlify(inBuffer).decode('UTF-8')
    inBuffer = [inBuffer[i:i+2] for i in range(0, len(inBuffer), 2)]
    return inBuffer


def setCurrentA(current):
    '''set current, expects float value in Ampere. There is an offset of 0.1A which is corrected in tthis function'''
    global DevNode
    global iNom
    global pause
    offset = 0.1 #measured offset with fluke 80i-110s

    SD = b'\xD1'
    DN = bytes.fromhex(DevNode)
    OBJ = b'\x33'
    setValue = hex(int(np.round((offset + current)*25600.0/iNom))).replace("0x","").zfill(4)
    print(setValue)
    DATA1 = bytes.fromhex(setValue[:2])
    DATA2 = bytes.fromhex(setValue[2:])
    CS = checksum([SD, DN, OBJ, DATA1, DATA2])
    get_query = SD+DN+OBJ+DATA1+DATA2+CS
    ser.write(get_query)
    return 0;


def setPowerA(power):
    '''set power, expects float value in Watts. Power accuracy of < 2% so I implemented a feedback loop to establish a more accurate voltage setting based on the difference between measured and setted value'''
    global DevNode
    global pNom
    global pause
    correctedPower = power

    for x in range(20):
        SD = b'\xD1'
        DN = bytes.fromhex(DevNode)
        OBJ = b'\x34'
        setValue = hex(int(np.round(correctedPower*25600.0/pNom))).replace("0x","").zfill(4)
        print(setValue)
        DATA1 = bytes.fromhex(setValue[:2])
        DATA2 = bytes.fromhex(setValue[2:])
        CS = checksum([SD, DN, OBJ, DATA1, DATA2])
        get_query = SD+DN+OBJ+DATA1+DATA2+CS
        ser.write(get_query)
        correctedPower = getPowerA() + 0.08*(power - getActualValues()[2])
    return 0;


def setCCMode():
    global DevNode
    global pause

    SD = b'\xD1'
    DN = bytes.fromhex(DevNode)
    OBJ = b'\x36'
    setValue = hex(0x0E00).replace("0x","").zfill(4)
    DATA1 = bytes.fromhex(setValue[:2])
    DATA2 = bytes.fromhex(setValue[2:])
    CS = checksum([SD, DN, OBJ, DATA1, DATA2])
    get_query = SD+DN+OBJ+DATA1+DATA2+CS
    ser.write(get_query)
    return 0;


def setCVMode():
    global DevNode
    global pause

    SD = b'\xD1'
    DN = bytes.fromhex(DevNode)
    OBJ = b'\x36'
    setValue = hex(0x0E02).replace("0x","").zfill(4)
    DATA1 = bytes.fromhex(setValue[:2])
    DATA2 = bytes.fromhex(setValue[2:])
    CS = checksum([SD, DN, OBJ, DATA1, DATA2])
    get_query = SD+DN+OBJ+DATA1+DATA2+CS
    ser.write(get_query)
    return 0;


def setCPMode():
    global DevNode
    global pause

    SD = b'\xD1'
    DN = bytes.fromhex(DevNode)
    OBJ = b'\x36'
    setValue = hex(0x0E04).replace("0x","").zfill(4)
    DATA1 = bytes.fromhex(setValue[:2])
    DATA2 = bytes.fromhex(setValue[2:])
    CS = checksum([SD, DN, OBJ, DATA1, DATA2])
    get_query = SD+DN+OBJ+DATA1+DATA2+CS
    ser.write(get_query)
    return 0;


def setCR1Mode():
    global DevNode
    global pause

    SD = b'\xD1'
    DN = bytes.fromhex(DevNode)
    OBJ = b'\x36'
    setValue = hex(0x0E6).replace("0x","").zfill(4)
    DATA1 = bytes.fromhex(setValue[:2])
    DATA2 = bytes.fromhex(setValue[2:])
    CS = checksum([SD, DN, OBJ, DATA1, DATA2])
    get_query = SD+DN+OBJ+DATA1+DATA2+CS
    ser.write(get_query)
    return 0;


def setCR2Mode():
    global DevNode
    global pause

    SD = b'\xD1'
    DN = bytes.fromhex(DevNode)
    OBJ = b'\x36'
    setValue = hex(0x0E08).replace("0x","").zfill(4)
    DATA1 = bytes.fromhex(setValue[:2])
    DATA2 = bytes.fromhex(setValue[2:])
    CS = checksum([SD, DN, OBJ, DATA1, DATA2])
    get_query = SD+DN+OBJ+DATA1+DATA2+CS
    ser.write(get_query)
    return 0;

def setRemoteControllOn():
    '''set load controll, bit 0 for switching input (1 = on), bit 3-1 regulation mode (000 = CC, 001 = CV, 010 = CP, 011 = CR1, 100 = CR2), bit 4 set remote (1 = remote controll), bit 6-5 control mode (00 = level A, 01 = Battery, 10 = level A/B, 11 = level B). Two byte register but one byte data'''
    global DevNode
    global pause

    SD = b'\xD1'
    DN = bytes.fromhex(DevNode)
    OBJ = b'\x36'
    setValue = hex(0x1010).replace("0x","").zfill(4)
    DATA1 = bytes.fromhex(setValue[:2])
    DATA2 = bytes.fromhex(setValue[2:])
    CS = checksum([SD, DN, OBJ, DATA1, DATA2])
    get_query = SD+DN+OBJ+DATA1+DATA2+CS
    ser.write(get_query)
    return 0;

def setRemoteControllOff():
    '''set load controll, bit 0 for switching input (1 = on), bit 3-1 regulation mode (000 = CC, 001 = CV, 010 = CP, 011 = CR1, 100 = CR2), bit 4 set remote (1 = remote controll), bit 6-5 control mode (00 = level A, 01 = Battery, 10 = level A/B, 11 = level B). Two byte register but one byte data'''
    global DevNode
    global vNom
    global pause

    SD = b'\xD1'
    DN = bytes.fromhex(DevNode)
    OBJ = b'\x36'
    setValue = hex(0x1000).replace("0x","").zfill(4)
    DATA1 = bytes.fromhex(setValue[:2])
    DATA2 = bytes.fromhex(setValue[2:])
    CS = checksum([SD, DN, OBJ, DATA1, DATA2])
    get_query = SD+DN+OBJ+DATA1+DATA2+CS
    ser.write(get_query)
    return 0;
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

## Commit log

2017-10-18 completed the questionnaire
    [questionnaire technique 2018.xlsx, questionnaire technique 2018_au.ods]
2017-10-19 added completed questionnaire in xlsx format
    [questionnaire technique 2018_au.xlsx]
2017-10-21 added info on transmission chains
2017-10-22 started market research on motors
2017-10-24 updated route to start from Chamonix instead of Chambery, added some comments in the readme
2017-10-24 added picture of raf van hulle's bike of 2015
2017-10-24 added second picture of raf van hulle's 2015 bike
2017-10-25 added new folders and changed some minor things
    [questionnaire technique 2018_au.xls]
2017-10-26 added info on possible solar cells and motor controller
2017-10-26 added info on tyres and solar cells
2017-11-02 added Victron MPPT charge controller
2017-11-13 added dropout dimensions for rear wheel
2017-11-24 added sw frame parts
    [Part1.SLDPRT, Part4.SLDPRT, frame-eyelets.SLDPRT]
2017-11-24 added frame drawings
    [Part1.SLDPRT, Part2.SLDPRT, Part4.SLDPRT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]
2017-11-25 addded all parts and assembly
    [Part1.SLDPRT, Part2.SLDPRT, Part4.SLDPRT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]
2017-11-25 adjusted rear frame eyelets to be more accurate
    adjusted rear frame eyelets to be more accurate by about 3 mm
2017-11-25 updated part namings and remade assembly
    [Assembly.SLDASM, Part1.SLDPRT, Part3.SLDPRT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]
2017-11-25 updates on frame and assembly
    Quick hack on Part 2 to get matching with Part 3. Part 2 has to be checked for dimensions because it appears to have slight mismatches.
    [Assembly.SLDASM, Part2.SLDPRT, Part3.SLDPRT]
2017-11-25 added 20 inch weel part and updated assembly
    [20 inch wheel.SLDPRT, Assembly.SLDASM]
2017-11-27 added chair
    [stoeltje2.SLDPRT]
2017-11-27 made new version of part 2.
    More accurate dimensions of part 2.
    Updated assembly with new part 2.
    [Assembly.SLDASM, Part2_new.SLDPRT, Part3.SLDPRT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]
2017-11-27 added things to purchase list
    drivetrain/rear-wheel stuff.
2017-11-29 frame DONE
    [Angular Contact Ball Bearing_68_ISO.sldprt, Angular Contact Ball Bearing_68_ISO_17X35X10_ISO 15 ABB - 1017 - 12,SI,NC,12_68.sldprt, Mirrorr_calf_new.sldprt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]
2017-12-11 Klemmen
    Klemmen toegevoegd
    [KlemZitjeVooraan-achterkant v2.step, KlemZitjeVooraan-eenvoudig v4.step, SpacersZitjeAchter v2.step]
2017-12-17 added sw aero sim
    [20 inch wheel simple.SLDPRT, Assembly_simple.SLDASM, GG Force (Z) 1_gm4_rf7_v10.xlsx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]
2017-12-20 added info on MPPT, purchase order for solar cells and info on BMS
2017-12-23 added sphere and cyclinder simulation results
    [Drag_coefficient_of_a_sphere_as_a_function_of_Reynolds_number.csv, drag_cylinder_ref.csv, simulated.csv]
2017-12-25 did a bunch of aero sims on roof test set ups
    [Assembly_simple.SLDASM, Mirrorsidefender.SLDPRT, global_parameters.txt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]
2017-12-27 flat roof case added
2018-01-02 simple frame assembly update (aero sim)
    [Assembly_simple.SLDASM, Part4.SLDPRT, global_parameters.txt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]
2018-01-06 added rear fearing
    [roof_test4.SLDPRT, staart_v1.SLDPRT]
2018-01-07 dimensioned flat roof to realistic dimensions
    [roof_test0.SLDPRT]
2018-01-09 made docs folder where all the blog material will go
2018-05-27 added sponsors to website
    [18650_littokala_baptist0000.csv, 18650_littokala_baptist0001.csv, 18650_littokala_baptist0002.csv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]
2018-05-27 removed checklist
    [questionnaire technique 2018.xls]
2018-09-06 sponsor text boltzmann update
